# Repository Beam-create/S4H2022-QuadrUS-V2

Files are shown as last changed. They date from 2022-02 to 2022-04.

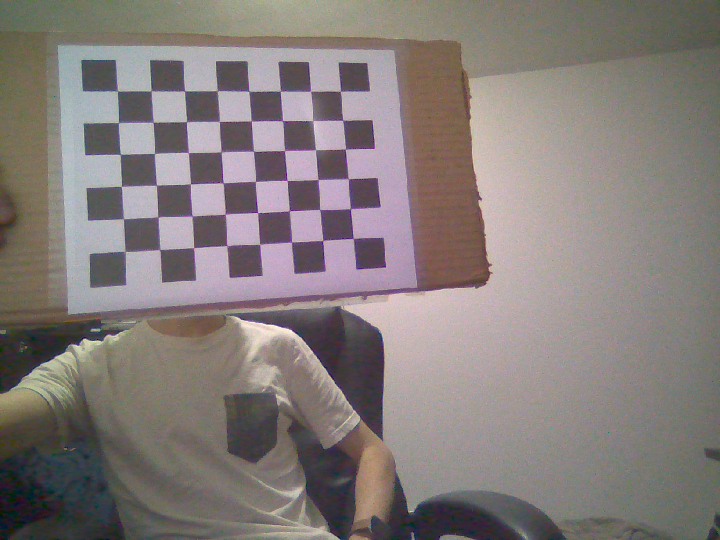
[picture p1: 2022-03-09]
VISION/CalibrationStereo/Images/Gauche/imgG22.png

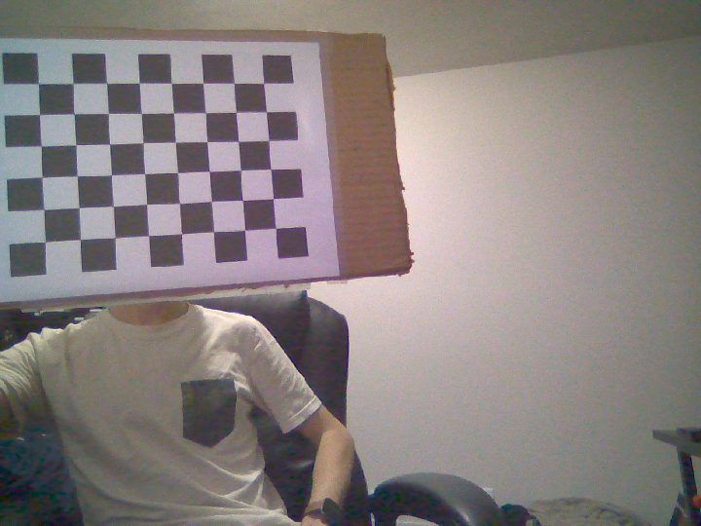
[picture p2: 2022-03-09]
VISION/CalibrationStereo/Images/Droite/imgD22.png

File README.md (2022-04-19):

# S4H2022-RufUS

### Robot-chien | UdeS-GRO
 

## Présentation du projet
<p align="center">
    	
    	<br>
    	
	<br>
	<a>Respectivement <strong>Antoine Waltz</strong>, <strong>Jordan Simard</strong>, <strong>Guillaume Blain</strong>, <strong>Mathieu Beaudoin</strong>, <strong>Christopher Pacheco</strong> et <strong>Nicolas Longchamps</strong></a>
</p>

<p align="center">
	
	<br>
</p>

RufUS est un robot collaboratif conçu et fabriqué par 6 étudiants en génie robotique à l'Université de Sherbrooke. Ce projet est fait dans le cadre du projet de la session 4.

Le but de ce projet est de construire un robot ayant la capacité de détecter, saisir puis rapporter un item. Pour ce faire, RufUS intègre une vision caméra, un bras robotique et une base mobile.

## Téléchargement du projet
1. Installez le fichier d'installation grâce à la commande ci-dessous:
 ```
 wget https://raw.githubusercontent.com/Beam-create/S4H2022-RufUS/main/Installation.sh
 ```
2. Exécutez le fichier grâce à cette commande:
 ```
 bash Installation.sh
 ```

> L'exécution du fichier permet d'installer automatiquement toutes les librairies ROS et les dépendances nécessaires au projet. Il permet aussi de configurer l'infrastructure ROS du projet. En effet, Un dossier sous le nom de rufus_ws (rufus workspace) contenant tous les éléments nécessaire au fonctionnement de la plateforme sera créé.
### Validation de l'installation
1. Ouvrir un terminal et exécutez cette commande:
```
gedit .bashrc
```
2. Allez à la fin du fichier
3. Validez que *source ~/rufus_ws/devel/setup.bash* ne se trouver par entre ( " " )
## Comment démarrer le projet
1. Suivre les instructions d'installation sur un ordinateur avec Ubuntu20.04.
2. Suivre les instructions d'installation de Ubuntu20.04 sur le Jetson Nano (Voir [Configuration du Jetson Nano](/VISION#configuration-du-jetson-nano))
3. Lorsque l'installation est terminée sur le Jetson Nano, configurez le hotspot (Voir [Création d'un hotspot](/ROS#création-dun-hotspot)).
4. Avec le hotspot configuré, connectez vous par SSH au Jetson Nano.
5. Une fois connecté, allez dans le dossier rufus_ws et exécutez une compilation du programme ROS :
```
cd ~/rufus_ws     
catkin_make
```
puis une fois compilé,
```
source devel/setup.bash
```
6. Ensuite, toujours sur le Jetson Nano avec la connexion SSH, lancez le programme *master* :
```
roslaunch rufus_master rufus_master.launch
```
7. Puis, avec l'ordinateur *remote*, lancez :
```
roslaunch rufus_remote rufus_remote.launch
```
puis, dans un autre terminal, lancez _rqt_ avec la commande :
```
rqt
```
Et le tour est joué! Vous obtiendrez ceci comme interface utilisateur :
<p align="center">
	
	<br>
</p>

**Troubleshooting**
Si des problèmes de connexion ont lieu, vérifiez que les adresses IP concordent avec les *launchfiles*.

## Table des matières
* Documentation
	* [Base](/FABRICATION/BASE#s4h2022-rufusbase)
		* [Fichiers CAD](/FABRICATION/BASE#fichers-cad)
		* [Comment fabriquer la base mobile](/FABRICATION/BASE#comment-fabriquer-la-base-mobile) 
			* [Liste des matériaux et composantes](/FABRICATION/BASE#liste-des-matériaux-et-composantes)
			* [Assemblage mécanique](/FABRICATION/BASE#assemblage-mécanique)
			* [Assemblage électrique](/FABRICATION/BASE#assemblage-électrique)
	* [Bras](/BRAS.md)
		* [Assemblage du bras robot](/BRAS.md#assemblage-du-bras-robot)
		* [Contrôle du bras robot](/BRAS.md#contrôle-du-bras-robot)
		* [Dépendances logicielles](/BRAS.md#dépendances-logicielles)
	* [Vision](/VISION#s4h2022-rufusvision)
		* [Matériel nécessaire](/VISION#matériel-nécessaire)
		* [Configuration du Jetson Nano](/VISION#configuration-du-jetson-nano)
			* [Installation de Ubuntu 20.04](/VISION#installation-de-ubuntu-2004)
			* [Installation des dépendances (vision)](/VISION#installation-des-dépendances)  
	* [Arduino](/ARDUINO#s4h2022-rufusarduino)
	* [ROS](/ROS#s4h2022-rufusros)
		* [Configuration du Jetson Nano](/ROS#configuartion-du-jetson-nano) 
			* [Création d'un hotspot](/ROS#création-dun-hotspot)
			* [Connexion par ssh](/ROS#connexion-au-jetson-nano-par-ssh) 
* [Licence](https://github.com/Beam-create/S4H2022-RufUS/blob/main/README.md#licence-mit)

### Licence MIT
Copyright 2022 RufUS

Permission is hereby granted, free of charge, to any person obtaining a copy of this software and associated documentation files (the "Software"), to deal in the Software without restriction, including without limitation the rights to use, copy, modify, merge, publish, distribute, sublicense, and/or sell copies of the Software, and to permit persons to whom the Software is furnished to do so, subject to the following conditions:

The above copyright notice and this permission notice shall be included in all copies or substantial portions of the Software.

THE SOFTWARE IS PROVIDED "AS IS", WITHOUT WARRANTY OF ANY KIND, EXPRESS OR IMPLIED, INCLUDING BUT NOT LIMITED TO THE WARRANTIES OF MERCHANTABILITY, FITNESS FOR A PARTICULAR PURPOSE AND NONINFRINGEMENT. IN NO EVENT SHALL THE AUTHORS OR COPYRIGHT HOLDERS BE LIABLE FOR ANY CLAIM, DAMAGES OR OTHER LIABILITY, WHETHER IN AN ACTION OF CONTRACT, TORT OR OTHERWISE, ARISING FROM, OUT OF OR IN CONNECTION WITH THE SOFTWARE OR THE USE OR OTHER DEALINGS IN THE SOFTWARE.

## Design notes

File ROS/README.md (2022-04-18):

# S4H2022-RufUS/ROS

## Configuration du Jetson Nano
### Création d'un hotspot
La création d'un réseau wi-fi dit "hotspot" sur un appareil permet à un ordinateur tiers de se connecter à cet appareil et d'avoir accès à l'internet sans fil si l'appareil recoit une connexion internet filaire. Par extension, cela permet à l'ordinateur tiers d'accéder au terminal de l'appareil par "ssh" afin de lancer des commandes (voir la section correspondante). Le but ici est donc de lancer les commandes ROS sur le Jetson Nano à partir d'un autre ordinateur sans connexion filaire reliant les deux appareils.
##### Méthode 1 (simple)
1. Aller dans la section "Wi-Fi" des paramètres de Ubuntu du Jetson Nano
2. Appuyer sur les trois petits points en haut à droite de la fenêtre, puis sélectionner "Allumer le point d'accès Wi-Fi..."

3. Assigner un nom au réseau (au choix), définir un mot de passe (au choix) et appuyer sur "Allumer"

4. Vérifier si le hotspot apparait parmi les réseaux disponible sur l'ordinateur, le cas échéant, s'y connecter

#### Méthode 2 (plus d'options)
1. Ouvrir un terminal de commande sur le Jetson Nano, puis taper la commande "nm-connection-editor": la fenêtre "Connexions réseau" devrait apparaître

2. Appuyer sur "+" en bas à gauche de la fenêtre pour ajouter un nouveau réseau

3. Sélectionner "Wi-Fi" dans les options de la fenêtre "Sélectionner un type de connexion", puis appuyer sur "Créer"

4. Modifier au minimum ces paramètres dans l'onglet "Wi-Fi":
	*   Assigner un nom à la connexion (au choix)
	*  Assigner un SSID (au choix)à
	* Sélectionner le mode "Hotspot"

5. Optionnel: Modifier les autres paramètres selon les besoins
6. Appuyer sur "Enregistrer"
7. Aller dans la section "Wi-Fi" des paramètres de Ubuntu du Jetson Nano
8. Appuyer sur les trois petits points en haut à droite de la fenêtre, puis sélectionner "Connexion à un réseau masqué..."

9. Sélectionner le hotspot créé en fonction du nom assigné à l'étape 4, puis appuyer sur "Se connecter"

10. Vérifier si le hotspot apparait parmi les réseaux disponible sur l'ordinateur, le cas échéant, s'y connecter

### Connexion au Jetson Nano par SSH
1. Ouvrir un terminal de commande sur le Jetson Nano et taper "ifconfig"
2. Noter l'adresse ip à côté de "inet" sous "wlan0" de la forme 10.x.x.x, par exemple 10.42.0.1
3. Ouvrir un terminal de commande sur l'ordinateur et taper "ssh <Nom du Jetson Nano>@<Adresse ip notée>", par exemple "ssh jetson@10.42.0.1"
4. Accepter les demandes d'accès et entrer le mot de passe du Jetson Nano le cas échéant

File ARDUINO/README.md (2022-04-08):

# S4H2022-RufUS/Arduino
On retrouve ici la documentation concernant le projet *platformIO*. Si vous n'êtes pas familier avec cet extension de *visual studio code* (vscode), nous vous recommendons de vous rendre sur la [page officielle](https://docs.platformio.org/en/latest/what-is-platformio.html) pour de plus amples informations. Il est recommendé de l'installer directement à partir de l'onglet extensions dans vscode.

## Configuration
Il suffit tout simplement d'ouvrir le dossier contenant le fichier *platformio.ini* dans vscode et de téléverser le fichier main.cpp dans votre arduino mega 2560.

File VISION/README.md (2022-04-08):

# S4H2022-RufUS/VISION
## Matériel nécessaire
- [ ] **Caméra stéréoscopique:**   [IMX219-83](https://www.waveshare.com/wiki/IMX219-83_Stereo_Camera) 
## Configuration du Jetson Nano
### Installation de Ubuntu 20.04 
D'ici la sortie d'une version de JetPack (OS de base du Jetson Nano) utilisant Ubuntu 20.04.

Suivre le [tutoriel de QEngineering](https://qengineering.eu/install-ubuntu-20.04-on-jetson-nano.html) afin d'installer et de configurer le Jetson Nano.

**Une image précompilée (qui ne nécessite pas de "*build from source*") est disponible [ici](https://github.com/Qengineering/Jetson-Nano-Ubuntu-20-image), par QEngineering également.**

On conseille l'image précompilée, qui ne prendra pas 6 heures de "*build*".
### Installation des dépendances
Pour les installations nécessaires (python3),

    pip3 install matplotlib numpy pillow imutils mediapipe 

#### Dual_Detect.py
Ce programme permet de détecter la présence d'un visage et d'une balle de jaune ou orange. Ensuite, par triangulation, la distance est évaluée et renvoyée en cm sur l'image.

    python3 DualDetect.py

#### test_vpi.py 
Ce programme évalue la disparité stéréoscopique et retourne une image de style *heatmap*. Il fonctionne pour le moment avec python2.7.

Afin de faire fonctionner la librairie VPI de NVIDIA pour l'utilisation de CUDA dans l'évaluation de la disparité, on doit créer un lien symbolique dans Ubuntu 20.04:

    cd /usr/lib/python2.7/dist-packages
    sudo ln -s /opt/nvidia/vpi1/lib64/python/vpi.so
Finalement, on doit modifier le fichier .bashrc afin d'éviter une erreur de dépendance :

**Afin d'ouvrir le fichier .bashrc:**

    sudo nano ~/.bashrc

Ajouter à la fin du .bashrc :

    export LD_PRELOAD=/usr/lib/aarch64-linux-gnu/libgomp.so.1
Sauvegarder et quitter le fichier. Le Jetson est maintenant prêt!

**Pour exécuter le programme test_vpi.py**

    python2 test_vpi.py

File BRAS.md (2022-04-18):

# S4H2022-RufUS/BRAS
## Liste des matériaux et composantes
- [ ] 1 x Servo DS3225  ([amazon](https://www.amazon.ca/-/fr/enti%C3%A8rement-m%C3%A9tallique-num%C3%A9rique-voitures-contr%C3%B4le/dp/B07NSG5WFQ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))
- [ ] 2 x Servo DS3218 ([amazon](https://www.amazon.ca/Servomoteur-num%C3%A9rique-%C3%A9tanche-voiture-contr%C3%B4le/dp/B07MDM1C3M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))
- [ ] 1 x Servo SG90 ([amazon](https://www.amazon.ca/-/fr/servomoteur-radiocommand%C3%A9-h%C3%A9licopt%C3%A8re-v%C3%A9hicules-compatible/dp/B097RD8RB7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))
## Assemblage du bras robot

[Instructions de montage du bras.pdf](https://github.com/Beam-create/S4H2022-RufUS/files/8430149/Instructions.de.montage.du.bras.pdf)

Voici le site sur lequel ces instructions sont basés : [lien](http://www.eezyrobots.it/eba_mk2.html)

Tout crédit pour le modèle utilisé se réserve à: Carlo Franciscone, daGHIZmo ([profil thingiverse]( https://www.thingiverse.com/daghizmo/designs)).

Certaines modifications au niveau du dimensionnement ont été apportés afin de répondre au besoin du projet RufUS: 
 1- Assise de servo moteur.
 2- Longueur des membrures.

Lien pour la license CC: https://www.thingiverse.com/thing:1454048

## Contrôle du bras robot

### Cinématique inverse
Afin de se rendre à la position cartésienne de la balle (position détecté par la caméra), une cinématique inverse a été modélisée à partir des schéma suivant :

1- Vue de coter du bras du robot :
vue_coter2

2- Vue de dessus du bras du robot : 
vue_dessus2

Les équations tirés de ces schémas sont :
<p align="center">
    
    <br>
    
    <br>
    
</p>

Avec la position en "x" et en "z" de la balle, il est possible de déterminer l'angle de rotation du joint 1. Par la suite, une fois que l'angle 1 est connu, il est possible d'utiliser le "solver" "nsolve" de python pour résoudre le système à deux équations et 2 inconnues pour trouver la valeur des angles pour les joints 2 et 3. Les valeurs de pi/2 et 0 dans le "nsolve" représente les valeurs des angles initiales en radians des joints 2 et 3 respectivement, ce qui permet d'accélérer la résolution du système d'équation.

### Calibration des servo
Afin de bien modéliser le comportement réel des servos moteurs, une calibration est utilisée dans le but d'extraire une fonction approximative du signal PWM en fonction de l'angle désiré. 

Les étapes de calibration sont :

 1- Création d'une série de données [angles_réels, PWM_envoyés] pour chaque servo.

 2- Selon l'allure de la courbe, on utilise une fonction de linéarisation à plusieurs coefficients afin d'approximer la courbe de données discrètes. 

 3- Mesurer les erreurs quadratiques afin d'assurer une précision adéquate.

 4- Modéliser la fonction de *writeMicroseconds()* selon la fonction linéarisée obtenue.

> Pour ce faire, Matlab/Python sont de bons outils d'analyse numérique. 

## Dépendances logicielles
Pour le fonctionnement bas-niveau du bras, le code c++ doit inclure la librairie externe suivante:

1- [Servo.h](https://github.com/arduino-libraries/Servo), librairie Arduino pour le contrôle de servo moteur selon une commande PWM ou un angle.

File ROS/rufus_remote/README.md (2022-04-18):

# Fonctionnement du package

Le package rufus_remote doit être présent dans l'ordinateur connecté au master
Ce package contient les scripts pour le contrôle de la base et du bras, et le launch file pour se connecter au robot

## Nodes:

Le package contient le cde source des nodes suivantes:
- base_teleop
- bras_teleop

## Launch files

Le launch file pour connecter l'ordinateur au robot est:
rufus_remote.launch

La commande pour partir le laucnh file est:

    roslaunch rufus_remote rufus_remote.launch

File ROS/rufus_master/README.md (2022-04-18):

# Fonctionnement du package

Le package rufus_master doit être téléchargé dans le Jetson Nano. Ce package contient les scripts pour le contrôle de la base et le launch file pour démarer le robot

## Messages:

Le package crée les messages suivants:

-   bras_commands.msg
-   Feedback_arduino_msgs.msg
-   Rufus_base_msgs.msg

## Nodes:

Le package contient le cde source des nodes suivantes:

-   base_control_node

## Launch files

Le launch file pour démarrer le robot est:
rufus_master.launch

La commande pour partir le laucnh file est: 

    roslaunch rufus_master rufus_master.launch

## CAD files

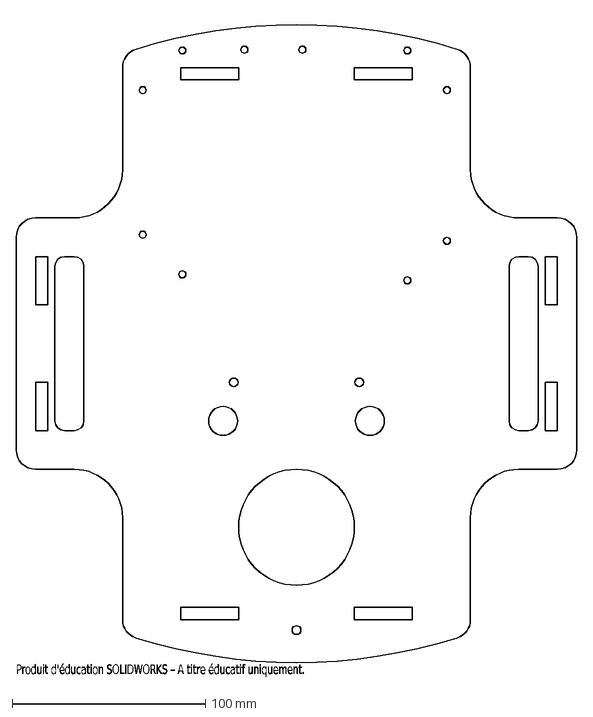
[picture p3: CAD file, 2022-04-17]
FABRICATION/BASE/DÉCOUPER/S4H2022_Base_002.DXF
Produit d'éducation SOLIDWORKS – A titre éducatif uniquement.

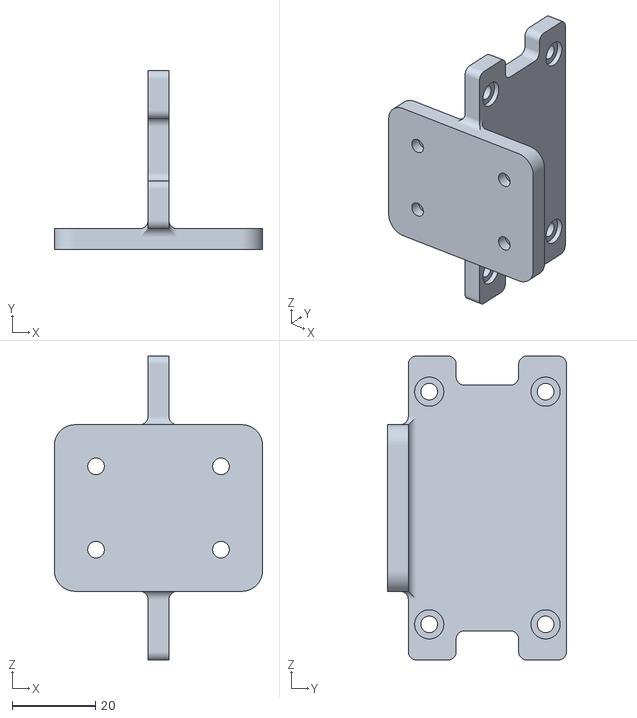
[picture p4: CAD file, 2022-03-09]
FABRICATION/BASE/IMPRIMER/S4H2022_Base_drive_bracket_V3.STL
50.0 x 43.0 x 73.0

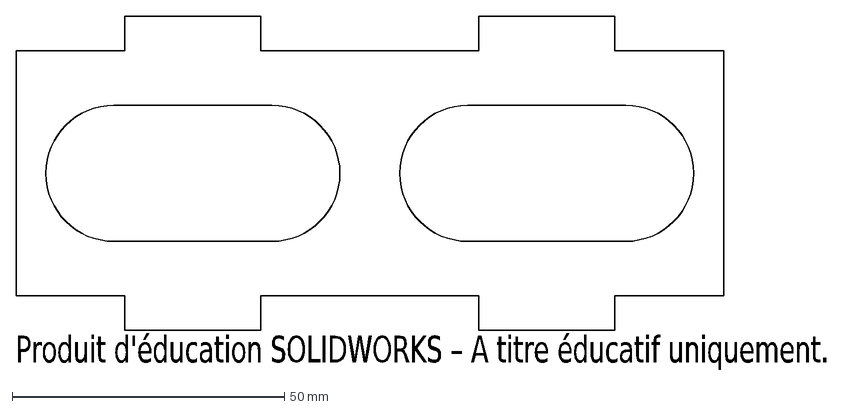
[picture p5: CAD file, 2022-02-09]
FABRICATION/BASE/DÉCOUPER/S4H2022_Base_004.DXF
Produit d'éducation SOLIDWORKS – A titre éducatif uniquement.

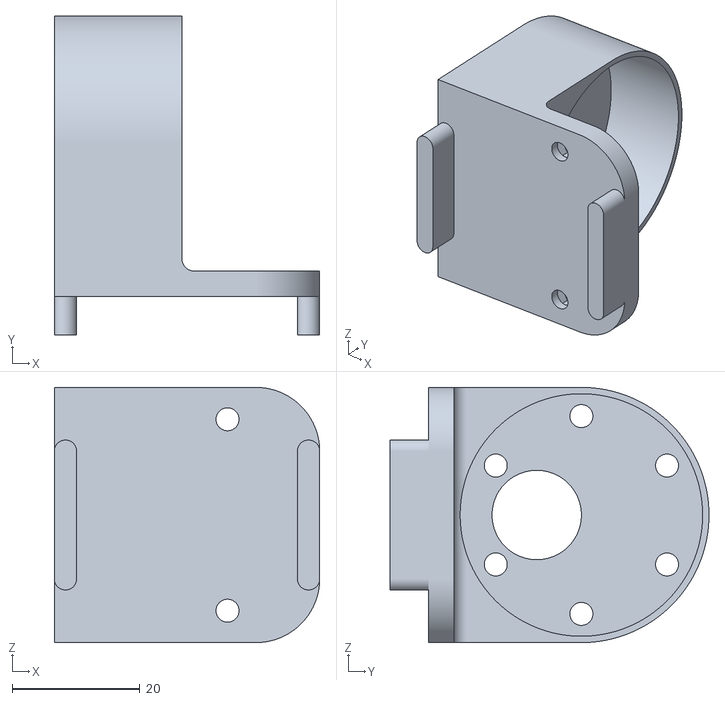
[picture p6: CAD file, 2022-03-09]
FABRICATION/BASE/IMPRIMER/S4H2022_Base_motor_mount.STL
41.6 x 50.0 x 40.0

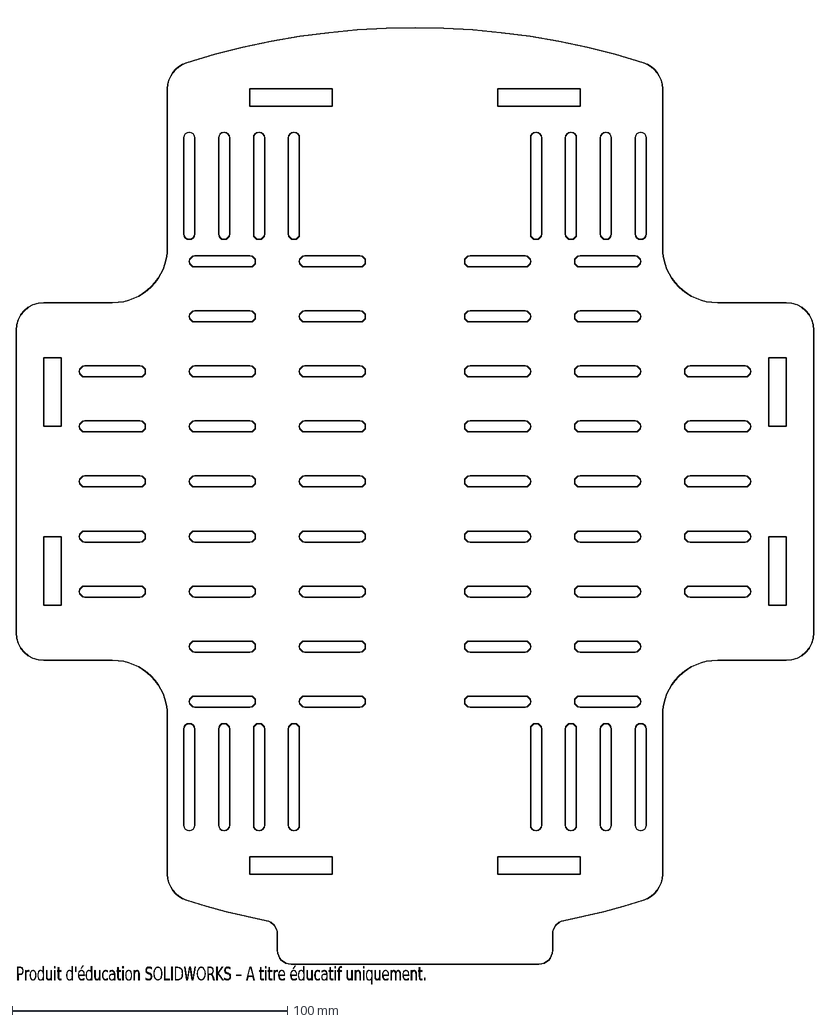
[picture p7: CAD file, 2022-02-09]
FABRICATION/BASE/DÉCOUPER/S4H2022_Base_001.DXF
Produit d'éducation SOLIDWORKS – A titre éducatif uniquement.

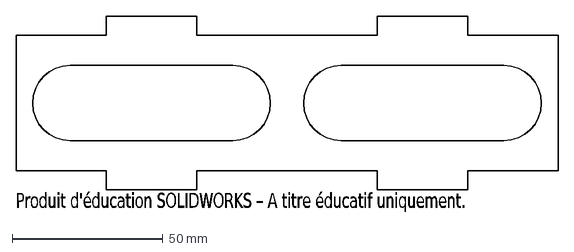
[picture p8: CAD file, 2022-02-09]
FABRICATION/BASE/DÉCOUPER/S4H2022_Base_003.DXF
Produit d'éducation SOLIDWORKS – A titre éducatif uniquement.

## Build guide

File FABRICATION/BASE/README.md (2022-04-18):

# S4H2022-RufUS/BASE
## [Fichiers CAD](https://github.com/Beam-create/S4H2022-RufUS/tree/main/CAD)

## Comment fabriquer la base mobile
Base_mec_cool

La base mobile est faite de matériaux et de composants faciles à trouver. Sa réalisation nécessite l'accès à une **découpeuse laser à bois**, une **imprimante 3d** et des outils électroniques tels qu'un **fer à souder**, un **multimètre** et une **source d'alimentation 12V** (optionnel).

### Liste des matériaux et composantes
***
#### Mécanique
- [ ]  Vis M3 X 0.5 
- [ ] Écrous M3 X 0.5 
- [ ] 2' X 3' X 1/4" contre-plaqué
- [ ] Roue Mecanum 80mm ([robotshop](https://www.robotshop.com/ca/en/80mm-mecanum-wheel-kit-4x.html))
- [ ] Moteur Pololu 50:1 12VDC  ([pololu](https://www.pololu.com/product/4753))
- [ ] Moyeu Servocity 1/4"  ([servocity](https://www.servocity.com/0-250-0-770-set-screw-hub/))
- [ ] Support moteur Pololu ([pololu](https://www.pololu.com/product/1084))

### Électrique
- [ ] Arduino Mega 2560 ([arduino](https://store-usa.arduino.cc/products/arduino-mega-2560-rev3))
- [ ] Contrôleur Cytron MD13s ([cytron](https://www.cytron.io/p-13amp-6v-30v-dc-motor-driver))
- [ ] Convertisseur DC-DC ([amazon](https://www.amazon.ca/Yizhet-Module-dalimentation-r%C3%A9glable-LM2596/dp/B08Q2YKJ6Q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))
- [ ] Ensemble connecteurs Dupont ([amazon](https://www.amazon.ca/Yangoutool-Dupont-connecteurs-cliquet-JST-XH/dp/B07X9MJ8G2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))
- [ ] Ensemble espaceur PCB ([amazon](https://www.amazon.ca/Litorange-entretoises-hexagonales-femelle-circuit/dp/B07TP2YYQB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))
- [ ] Fil 22 awg ([robotshop](https://www.robotshop.com/ca/fr/kit-fils-pvc-noyau-solide-plusivo-22awg-6-couleurs-10-m-chacun.html))
- [ ] Pin header([amazon](https://www.amazon.ca/-/fr/10-Paire-femelle-broches-Connecteur-Arduino/dp/B019WOPOHI/ref=sr_1_10?__mk_fr_CA=ÅMÅŽÕÑ&crid=2QZMUE8YLUWN3&keywords=pin+header&qid=1649268265&sprefix=pin+header%2Caps%2C54&sr=8-10))
- [ ] Connecteur bornier([amazon](https://www.amazon.ca/-/fr/gp/product/B07H5G7GC6/ref=ppx_yo_dt_b_asin_title_o07_s00?ie=UTF8&th=1))
- [ ] Connecteur grove([amazon](https://www.amazon.ca/-/fr/WOWOONE-connecteurs-femelles-Micro-broches/dp/B08RHGT3W3/ref=sr_1_38?__mk_fr_CA=ÅMÅŽÕÑ&crid=2IVHVETWWB96F&keywords=grove+connectors+4&qid=1649268329&sprefix=grove+connectors+4%2Caps%2C57&sr=8-38))

### Assemblage mécanique
***
Ce [dossier](https://github.com/Beam-create/S4H2022-RufUS/tree/main/CAD) contient plus de détails sur l'assemblage, ainsi que les STL et DXF pour fabriquer les pièces.
#### Assemblage châssis
S4H2022_Base_000

#### Assemblage roues
S4H2022_Base_wheel_assy

### Assemblage électrique
***
Base_elec

#### Circuit imprimé


Un PCB a été concu afin de facilliter les branchements électriques. Toute l'information reliée au sens des branchements est indiqué directement sur le circuit. Pour se procurer le PCB, il suffit d'aller sur un site de commande de pcb en ligne (ex: [jlcpcb.com](https://jlcpcb.com/VGB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)) et d'y téléverser le dossier compressé  [*PCB_Production.zip*](https://github.com/Beam-create/S4H2022-RufUS/files/8502373/PCB_Production.zip). Aucun paramètre par défaut n'est à modifier.

> **IMPORTANT**: Pour la section de pin à souder située à droite du Arduino Mega, il faut SEULEMENT souder les pins entourées en rouge.

##### Configuration des convertisseurs DC-DC
1. Brancher une source de tension (12V) à l'entré du convertisseur et brancher un multimetre à sa sortie
2. À l'aide d'un tournevis, vous devez changer la tension de sortie à 5V et à 6.8V pour deux convertisseurs que vous pourrez ensuite placer sur le pcb aux endroits indiqués.

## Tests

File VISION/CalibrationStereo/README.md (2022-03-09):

# Calibration de la caméra stéréoscopique
 1. Se rendre dans le répertoire **CalibrationStereo**
	`cd CalibrationStereo`
## Acquisition
Afin de calibrer la caméra stéréoscopique, on doit utiliser un échiquier de calibration.
Après l'impression sur une feuille 8½x11, on puet exécuter la calibration avec :
   ` python3 Acquisition.py`
Afin d'enregistrer une image, on appuie sur la touche `ESPACE`, pour quitter l'application, on appuie sur la touche `q` ou `ESC`.

## Calibration
Lorsque la totalité du champ de vision de la caméra a été couvert par des photos de l'échiquier, on puet poursuivre avec la calibration.
La calibration consiste à premièrement rectifier les images individuellement afin d'éliminer la distorsion causée par la lentille, puis à calibrer la stéréoscopie.
Il suffit d'exécuter :

    python3 StereoCalibration.py
Les données de calibration seront ainsi enregistrées sous **stereoMap.xml**.

## Test de la calibration
Afin d'évaluer la qualité de la calibration, on peut exécuter le programme **StereoVision_RectificationTest.py**.
`python3 StereoVision_RectificationTest.py`

Si la calibration est erronée, on peut refaire l'acquisition. Le processus est très itératif.

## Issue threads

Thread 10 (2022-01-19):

Contrôle en vitesse et position PID

Beam-create, 2022-01-19:

Chrispako990210, 2022-01-26:
Nb d'heures :
Risques :
Problèmes :

Chrispako990210, 2022-02-16:
This issue should be deleted, it is not implemented in the project dev.

Closed 2022-02-16.

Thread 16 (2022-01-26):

Stabilisateur mécanique pour la vision

NicoLongfield, 2022-01-26:
Concevoir un "gimbal" qui stabilisera la caméra stéréoscopique :

- [ ] Modélisation

- [ ] Assemblage

- [ ] Acquisition de données (accéléromètre)

- [ ] Prototypage électrique

- [ ] Développement logiciel de contrôle

NicoLongfield, 2022-01-26:
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

Closed 2022-02-23.

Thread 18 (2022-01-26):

Acquisition des données de l'accéléromètre

NicoLongfield, 2022-01-26:

Blain354, 2022-02-01:
le gyro sur la caméra fonctionne sur l'environnement linux (pi/jetson) mais pas sur arduino donc on utilise maintenant un gyro indépendant de la caméra qui est fonctionnel avec arduino

Closed 2022-02-16.

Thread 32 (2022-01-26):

Construire l'environnement de simulation ROS

Chrispako990210, 2022-01-26:

simj5121, 2022-01-26:
Nb d'heures : (Sem. 24-28 janv 0 heures),
Risques :
-Intégration des CAD
-Frottement entre les joints
Problèmes :

simj5121, 2022-02-01:
L'environnement global est terminer :
-Possible de faire bouger de manière indépendante chaque joint d'un robot simple à 3 axes

Closed 2022-02-01.

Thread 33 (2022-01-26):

Setup les CAD dans Gazebo + appliquer les  liens géométriques

Chrispako990210, 2022-01-26:

Chrispako990210, 2022-01-26:
Nb d'heures :
Risques : Bug d'intégration avec l'environnement de simulation
Problèmes :

Closed 2022-03-15.

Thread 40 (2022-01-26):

Faire une description gazebo de la base

Beam-create, 2022-01-26:

Beam-create, 2022-02-12:
Risque :  La base n'affiche pas complètement dans gazebo. Les roues ne sont pas affichés, mais aucun message d'erreur n'est affiché. Le debuggage peut prendre plus de temps que prévu

Closed 2022-03-09.

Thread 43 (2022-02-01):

Assemblage électrique de la base

Beam-create, 2022-02-01:

Beam-create, 2022-02-01:
BUG: Manque le convertisseur dc-dc 12v vers 6.8v

Je regarde avec François Ferland pour une solution. L'université va peut-être acheter des convertisseur puis nous les prêter.

Beam-create, 2022-02-01:
Difficile d'accès au compartiment électrique, il va falloir couper le châssis en bois et faire une barre de renforcement amovible. Il peut y avoir des complications pour couper ou pour solidifier le châssis.

Closed 2022-02-16.

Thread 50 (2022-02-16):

Redesign et print de la pince

Chrispako990210, 2022-02-16:

Closed 2022-02-16.

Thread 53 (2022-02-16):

Implémentation ros serial / rospy pour la com, jetson et arduino

Chrispako990210, 2022-02-16:

simj5121, 2022-03-14:
Création des nodes et des topics pour la communication avec le bras robot (position de la balle vue par la caméra et angles des joints du bras robot)

simj5121, 2022-03-22:
Problème : Intégration d'une librairie "custom" python dans ros -­> Résolue

Closed 2022-04-06.

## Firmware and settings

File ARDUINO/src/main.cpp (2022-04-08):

/* 
 * GRO 400 - Conception agile et ouverte en robotique
 * Code de démarrage
 * Auteurs: Antoine Waltz et al     
 * date: 22 février 2022
*/

/*------------------------------ Librairies ---------------------------------*/

#include <Arduino.h>
#include "rufus_lib/motor.h"
#include "rufus_lib/pid.h"
#include "rufus_lib/Bras_servo_control.h"
#include "Servo.h"
#include <ros.h>
#include <rufus_master/Rufus_base_msgs.h>
#include <rufus_master/bras_commands.h>
#include <std_msgs/String.h>
#include <rufus_master/Feedback_arduino_msgs.h>

/*------------------------------ Constantes ---------------------------------*/

#define BAUD            9600      // Fréquence de transmission serielle

/*---------------------------- variables globales ---------------------------*/
 
 // ENC_A: Fil jaune de l'encodeur, soit 2,3,18 ou 19
int FL_ENC_A_pin = 19;
int FR_ENC_A_pin = 18;
int BL_ENC_A_pin = 2;
int BR_ENC_A_pin = 3;

// ENC_B: Fil blanc de l'encodeur, entre 22 et 53 (30,32,34,36)
int FL_ENC_B_pin = 37;
int FR_ENC_B_pin = 35;
int BL_ENC_B_pin = 31;
int BR_ENC_B_pin = 33;

// ENC_Vcc: Fil bleu de l'encodeur, 3.5-20 V
// ENC_GND: Fil vert de l'encodeur

// DIR: Fil jaune du contrôleur de moteur, entre 22 et 53 (22,24,26,28)
int FL_DIR_pin = 27;
int FR_DIR_pin = 29;
int BL_DIR_pin = 23;
int BR_DIR_pin = 25;

// PWM: Fil blanc du contrôleur de moteur, entre 4 et 13 (4,5,6,7)
int FL_PWM_pin = 5;
int FR_PWM_pin = 4;
int BL_PWM_pin = 7;
int BR_PWM_pin = 6;

// Pin gimbal
int gimbal_pin = 8;


// Déclaration des objets moteur
motor FL_motor(FL_ENC_A_pin, FL_ENC_B_pin, FL_DIR_pin, FL_PWM_pin);
motor *FL = &FL_motor;
motor FR_motor(FR_ENC_A_pin, FR_ENC_B_pin, FR_DIR_pin, FR_PWM_pin);
motor *FR = &FR_motor;
motor BL_motor(BL_ENC_A_pin, BL_ENC_B_pin, BL_DIR_pin, BL_PWM_pin);
motor *BL = &BL_motor;
motor BR_motor(BR_ENC_A_pin, BR_ENC_B_pin, BR_DIR_pin, BR_PWM_pin);
motor *BR = &BR_motor;

// Déclaration de l'objet PID
PID pid(*FL, *FR, *BL, *BR);

// Déclaration de l'objet Gimbal
Servo gimbal;

// Declaration de l'objet Bras et autre variables
Bras_servo_control bras;
const long interpolTime = 7;
unsigned long currentTime;

// ROS
ros::NodeHandle nh;
rufus_master::Feedback_arduino_msgs feedback_msg;

/*------------------------- Prototypes de fonctions -------------------------*/

void readEncoderFL();
void readEncoderFR();
void readEncoderBL();
void readEncoderBR();
void commandCB(const rufus_master::Rufus_base_msgs& motor_cmd);
void brasCB(const rufus_master::bras_commands& bras_cmd);


/*---------------------------- fonctions "Main" -----------------------------*/

ros::Subscriber<rufus_master::Rufus_base_msgs> motor_sub("/rufus/base_arduino", commandCB);
ros::Subscriber<rufus_master::bras_commands> bras_sub("/rufus/bras_arduino", brasCB); // Get les commands via le topic envoyer par bras_teleop et IK
ros::Publisher arduino_feedback("/rufus/arduino_feedback",&feedback_msg);

void setup() {
  // Serial.begin(BAUD);

  // Setup ros, goes first always!
  nh.getHardware()->setBaud(57600);
  nh.initNode();
  nh.advertise(arduino_feedback);
  nh.subscribe(bras_sub);
  nh.subscribe(motor_sub);
  nh.negotiateTopics();


  // Fonctions qui assigne les pins à lire et les fonctions pour lire les encodeurs
  // attachInterrupt: 2, 3, 18, 19, 20, 21 (pins 20 & 21 are not available to use for interrupts while they are used for I2C communication)
  attachInterrupt(digitalPinToInterrupt(FL_motor.getPin(FL_motor._ENC_A)), readEncoderFL, RISING);
  attachInterrupt(digitalPinToInterrupt(FR_motor.getPin(FR_motor._ENC_A)), readEncoderFR, RISING);
  attachInterrupt(digitalPinToInterrupt(BL_motor.getPin(BL_motor._ENC_A)), readEncoderBL, RISING);
  attachInterrupt(digitalPinToInterrupt(BR_motor.getPin(BR_motor._ENC_A)), readEncoderBR, RISING);
  pid.setGains(1, 0.1, 0.05);
  gimbal.attach(gimbal_pin);
  gimbal.write(90); // Angle zéro à trouver, en degré

  bras.initServos();
  bras.drop();
  bras.goToHome();
}

void loop() {
  arduino_feedback.publish(&feedback_msg);
  nh.spinOnce();
  delay(10);
}

/*---------------------------Definition de fonctions ------------------------*/
// Fonctions qui appelle la fonction de lecture de la position de l'encodeur
void readEncoderFL(){
  FL_motor.readEncoder();
}
void readEncoderFR(){
  FR_motor.readEncoder();
}
void readEncoderBL(){
  BL_motor.readEncoder();
}
void readEncoderBR(){
  BR_motor.readEncoder();
}

void commandCB(const rufus_master::Rufus_base_msgs& motor_cmd)
{
  float cmd_FL = motor_cmd.motor_FL;
  float cmd_FR = motor_cmd.motor_FR;
  float cmd_BL = motor_cmd.motor_BL;
  float cmd_BR = motor_cmd.motor_BR;

  FL_motor.setPWM(cmd_FL);
  FR_motor.setPWM(cmd_FR);
  BL_motor.setPWM(cmd_BL);
  BR_motor.setPWM(cmd_BR);
  
  //Ajouter les fonctions pour faire tourner les moteurs en fonction des cmd_XX
  // pid.run(cmd_FL, cmd_FR, cmd_BL, cmd_BR);

  feedback_msg.motor_FL = cmd_FL;
  feedback_msg.motor_FR = cmd_FR;
  feedback_msg.motor_BL = cmd_BL;
  feedback_msg.motor_BR = cmd_BR;

}

void brasCB(const rufus_master::bras_commands& bras_cmd){ // Callback not triggered, A DEBUG!

  // Tsansfert des angles dans des variables locals
  float angles[nbJoints];
  angles[0] = bras_cmd.q1;
  angles[1] = bras_cmd.q2;
  angles[2] = bras_cmd.q3;


  bool isDone = false;
  float smoothAngles[nbJoints];
  if(bras_cmd.mode){
    bras.drop();
    while(!isDone){
      for (int i=0; i<nbJoints; i++)
      {
        smoothAngles[i] = (angles[i]*0.03) + (bras.prevAngles[i]*0.97);
        bras.prevAngles[i] = smoothAngles[i];
      }
      bras.goTo(smoothAngles);
      delay(7);
      if((round(smoothAngles[0]*100)/100.0) == angles[0] && (round(smoothAngles[1]*100)/100.0) == angles[1] && (round(smoothAngles[2]*100)/100.0) == angles[2]) // Sync once all 3 values have reached
      {
        isDone = true;
        bras.setPrevAngles(smoothAngles);
        // Serial.println("GOAL has been reached!"); //debugging
      }
    }
  }
  else{
    bras.goTo(angles);
  }
  // Check le state de leffecteur
  if(bras_cmd.effector){
    bras.pick();
    feedback_msg.effector = bras.isPick;
  }
  else{
    bras.drop();
    feedback_msg.effector = false;
  }

  // Gimbal control
  gimbal.write(bras_cmd.gimbalAng);

  
  feedback_msg.q1 = angles[0];
  feedback_msg.q2 = angles[1];
  feedback_msg.q3 = angles[2];
}

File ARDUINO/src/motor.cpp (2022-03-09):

/*
Projet S4 GRO 2022
Class to control Pololu 50:1 Metal Gearmotor 37Dx70L mm 12V 
with 64 CPR Encoder and with Cytron 13Amp 6V-30V DC Motor Driver 
on Arduino Mega 2560
@author Antoine Waltz et al
@version 1.0 09/02/2022
*/

#include "rufus_lib/motor.h"

motor::motor(){
    /*
    Constructeur par défaut qui assigne une valeur aux pins
    */
    _ENC_A_pin = -1;
    _ENC_B_pin = -1;
    _DIR_pin = -1;
    _PWM_pin = -1;
}
motor::motor(int ENC_A_pin, int ENC_B_pin, int DIR_pin, int PWM_pin){
    /*
    Constructeur qui vérifie la validité des pins entrées en paramètres et qui les assigne à ses attributs
    */
    if (motor::checkPins(ENC_A_pin, 1)){_ENC_A_pin = ENC_A_pin;}
    else{_ENC_A_pin = -1;}
    if (motor::checkPins(ENC_B_pin, 2)){_ENC_B_pin = ENC_B_pin;}
    else{_ENC_B_pin = -1;}
    if (motor::checkPins(DIR_pin, 3)){_DIR_pin = DIR_pin;}
    else{_DIR_pin = -1;}
    if (motor::checkPins(PWM_pin, 4)){_PWM_pin = PWM_pin;}
    else{_PWM_pin = -1;}
    motor::init();
}
motor::~motor(){
    /*
    Destructeur par défaut
    */
}
void motor::init(){
    /*
    Fonction qui initialise les pins sur l'Arduino
    */
    pinMode(motor::getPin(_ENC_A),INPUT);
    pinMode(motor::getPin(_ENC_B),INPUT);
    pinMode(motor::getPin(_DIR),OUTPUT);
    pinMode(motor::getPin(_PWM),OUTPUT);
}
bool motor::checkPins(int pin, int arg_nb){
    /*
    Fonction qui prend en paramètre une pin et son type selon 4 cas et qui vérifie si la pin fait partie des options disponible, retourne un booléen
    */
    switch (arg_nb){
        case 1:
            if (pin == 2 || pin == 3 || pin == 18 || pin == 19){
                return true;
            }
            else{
                Serial.println("Invalid pin number for _ENC_A_pin, choose either 2,3,18 or 19");
                return false;
            }
        case 2:
            if (pin >= 22 && pin <= 53){
                return true;
            }
            else{
                Serial.println("Invalid pin number for _ENC_B_pin, choose a pin between 22 and 53");
                return false;
            }
        case 3:
            if ((pin >= 22 && pin <= 53) || (pin >= 2 && pin <= 9) ){
                return true;
            }
            else{
                Serial.println("Invalid pin number for _DIR_pin, choose a pin between 22 and 53");
                return false;
            }
        case 4:
            if (pin >= 4 && pin <= 13){
            return true;
            }
            else{
                Serial.println("Invalid pin number for _PWM_pin, choose a pin between 4 and 13");
                return false;
            }
        default:
            Serial.println("Invalid pin number argument, choose between 1 and 4");
            return false;
        }
}
bool motor::safeCheck(){
    /*
    Fonction qui permet de vérifier si les pins ont bel et bien été assignées
    */
    if (motor::getPin(_ENC_A) == -1 || motor::getPin(_ENC_B) == -1 || motor::getPin(_DIR)== -1 || motor::getPin(_PWM) == -1) {return false;}
    else {return true;}
}
int motor::getPin(char _pinName[11]){
    /*
    Fonction qui retourne la valeur de la pin demandée
    */
    if (_pinName == _ENC_A){
        return _ENC_A_pin;
    }
    else if (_pinName == _ENC_B){
        return _ENC_B_pin;
    }
    else if (_pinName == _DIR){
        return _DIR_pin;
    }
    else if (_pinName == _PWM){
        return _PWM_pin;
    }
    else{
        Serial.println("Invalid pin name, choose either _ENC_A_pin, _ENC_B_pin, _DIR_pin or _PWM_pin");
        return -1;
    }
}
void motor::getPins(){
    /*
    Fonction qui affiche la valeur de toutes les pins
    */
    Serial.print(_ENC_A);
    Serial.print(" : ");
    Serial.println(_ENC_A_pin);
    Serial.print(_ENC_B);
    Serial.print(" : ");
    Serial.println(_ENC_B_pin);
    Serial.print(_DIR);
    Serial.print(" : ");
    Serial.println(_DIR_pin);
    Serial.print(_PWM);
    Serial.print(" : ");
    Serial.println(_PWM_pin);
}
void motor::readEncoder(){
    /*
    Fonction qui enregistre la position de l'encodeur sur un tour
    */
    if (digitalRead(_ENC_B_pin) > 0){
        encoder_pos++;
        }
    else {
        encoder_pos--;
        }
    if (encoder_pos >= encoder_max_pos){
        nb_rotation++;
        encoder_pos = encoder_pos - encoder_max_pos;
    }
    else if (encoder_pos <= -encoder_max_pos){
        nb_rotation--;
        encoder_pos = encoder_pos + encoder_max_pos;
    }
}
void motor::resetEncoder(){
    /*
    Fonction qui remet à zéro la position de l'encodeur
    */
    encoder_pos = 0;
    nb_rotation = 0;
}
int motor::getEncoderPos(){
    /*
    Fonction qui retourne la position de l'encodeur
    */
    return encoder_pos;
}
int motor::getNbRotation(){
    /*
    Fonction qui retourne le nombre de tours complets
    */
    return nb_rotation;
}
int motor::getEncoderPosTotal(){
    /*
    Fonction qui retourne la position absolue de l'encodeur depuis la dernière mise à zéro
    */
    return nb_rotation*encoder_max_pos + encoder_pos;
}
int motor::getResetEncoderPos(){
    /*
    Fonction qui retourne la position de l'encodeur sur un tour et qui réinitialise l'encodeur
    */
    int pos = motor::getEncoderPosTotal();
    motor::resetEncoder();
    return pos;
}
void motor::setPWM(float speed){
    /*
    Fonction qui permet de faire tourner le moteur selon un ratio de vitesse entre -1 et 1
    */
    set_speed = speed;
    int pwm = abs(speed*255.0f); // Change speed to unsigned integer
    // Switching polarity on DIR_PIN to change motor direction
    if (speed > 0) {
        digitalWrite(_DIR_pin, LOW);
    } else {
        digitalWrite(_DIR_pin, HIGH);
    }
    // SetPWM value
    analogWrite(_PWM_pin, (pwm > 255) ? 255 : static_cast<uint8_t>(pwm));
}
double motor::getMeanSpeed(){
    /*
    Fonction qui calcule et retourne la vitesse moyenne du moteur sur un intervalle de temps
    */
    int mean_time = 10; // ms, Temps entre deux lectures de l'encodeur pour calculer la vitesse moyenne
    int pos1 = motor::getEncoderPosTotal();
    delay(mean_time);
    int pos2 = motor::getEncoderPosTotal();
    return (double)((pos2-pos1))/(((mean_time))/1000.0)*pulse_per_seconds_to_unit_speed;
}

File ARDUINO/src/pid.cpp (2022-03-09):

/*
Projet S4 GRO 2022
Class to control Pololu 50:1 Metal Gearmotor 37Dx70L mm 12V 
with 64 CPR Encoder and with Cytron 13Amp 6V-30V DC Motor Driver 
on Arduino Mega 2560
@author Antoine Waltz et al
@version 1.0 09/02/2022
*/

#include "rufus_lib/pid.h"

PID::PID(motor &FL_motor, motor &FR_motor, motor &BL_motor, motor &BR_motor){
    _FL_motor = &FL_motor;
    _FR_motor = &FR_motor;
    _BL_motor = &BL_motor;
    _BR_motor = &BR_motor;
}
PID::~PID(){
    
}
void PID::setGains(float kp, float ki, float kd){
    Kp_ = kp; Ki_ = ki; Kd_ = kd;
}
void PID::reset(int motor_id){
    switch(motor_id){
        case 1:
            eIntegral_FL = 0;
            ePrevious_FL = 0;
            lastMeasureTime_FL = millis();
        case 2:
            eIntegral_FR = 0;
            ePrevious_FR = 0;
            lastMeasureTime_FR = millis();
        case 3:
            eIntegral_BL = 0;
            ePrevious_BL = 0;
            lastMeasureTime_BL = millis();
        case 4:
            eIntegral_BR = 0;
            ePrevious_BR = 0;
            lastMeasureTime_BR = millis();
    }
}
void PID::run(float cmd_FL,float cmd_FR,float cmd_BL,float cmd_BR){
    // Serial.println("Entré dans pid.run()");
    if (cmdPrevious_FL != cmd_FL){
        reset(1);
        atGoal_FL = false;
        atGoal_ = false;
        cmdPrevious_FL = cmd_FL;
    }
    else if (cmdPrevious_FR != cmd_FR){
        reset(2);
        atGoal_FR = false;
        atGoal_ = false;
        cmdPrevious_FR = cmd_FR;
    }
    else if (cmdPrevious_BL != cmd_BL){
        reset(3);
        atGoal_BL = false;
        atGoal_ = false;
        cmdPrevious_BL = cmd_BL;
    }
    else if (cmdPrevious_BR != cmd_BR){
        reset(4);
        atGoal_BR = false;
        atGoal_ = false;
        cmdPrevious_BR = cmd_BR;
    }
    // Serial.println("Vérification des commandes faite");
    // variables();
    //if (!atGoal_){
        // Serial.println("if (!atGoal_)");
        //if(!atGoal_FL){
            // Serial.println("if (!atGoal_FL)");
            double FL_error = cmd_FL - _FL_motor->getMeanSpeed();
            // Serial.println(FL_error);
            // Serial.println("Calcul de FL_error");
            Serial.println(FL_error);
            if(fabs(FL_error)<epsilon_){
                // Serial.println("if fabs(FR_error)<epsilon_)");
                atGoal_FL = true;
                _FL_motor->setPWM(cmd_FL);
            }
            else{
                // Serial.println("Entrée dans (*_FL_motor)->setPWM(computeCommand(1,FL_error))");
                _FL_motor->setPWM(computeCommand(1,FL_error));
                // Serial.println("(*_FL_motor)->setPWM(computeCommand(1,FL_error)) Fait!");
            }
        //}
        //if(!atGoal_FR){
            // Serial.println("if (!atGoal_FR)");
            double FR_error = cmd_FR - _FR_motor->getMeanSpeed();
            // Serial.println("Calcul de FR_error");
            // Serial.println(FR_error);
            if(fabs(FR_error)<epsilon_){
                // Serial.println("if fabs(FR_error)<epsilon_)");
                atGoal_FR = true;
                _FR_motor->setPWM(-cmd_FR);
            }
            else{
                _FR_motor->setPWM(computeCommand(2,FR_error));
            }
        //}
        //if(!atGoal_BL){
            // Serial.println("if (!atGoal_BL)");
            double BL_error = cmd_BL - _BL_motor->getMeanSpeed();
            if(fabs(BL_error)<epsilon_){
                atGoal_BL = true;
                _BL_motor->setPWM(cmd_BL);
            }
            else{
                _BL_motor->setPWM(computeCommand(3,BL_error));
            }
        //}
        //if(!atGoal_BR){
            // Serial.println("if (!atGoal_BR)");
            double BR_error = cmd_BR - _BR_motor->getMeanSpeed();
            if(fabs(BR_error)<epsilon_){
                atGoal_BR = true;
                _BR_motor->setPWM(-cmd_BR);
            }
            else{
                _BR_motor->setPWM(computeCommand(4,BR_error));
            }
        //}
        // if(atGoal_FL && atGoal_FR && atGoal_BL && atGoal_BR){
        //     atGoal_ = true;
        // }
    //}
    
}

float PID::computeCommand(int motor_id,double error){
    // Serial.println("computeCommand lancé");
    double eIntegral_;
    switch(motor_id){
        case 1:
            // Serial.println("computeCommand FL_motor");
            eIntegral_FL += error;
            eIntegral_ = eIntegral_FL;
            dt_ = (millis() - lastMeasureTime_FL)/1000.0;
        case 2:
            // Serial.println("computeCommand FR_motor");
            eIntegral_FR += error;
            eIntegral_ = eIntegral_FR;
            dt_ = (millis() - lastMeasureTime_FR)/1000.0;
        case 3:
            // Serial.println("computeCommand BL_motor");
            eIntegral_BL += error;
            eIntegral_ = eIntegral_BL;
            dt_ = (millis() - lastMeasureTime_BL)/1000.0;
        case 4:
            // Serial.println("computeCommand BR_motor");
            eIntegral_BR += error;
            eIntegral_ = eIntegral_BR;
            dt_ = (millis() - lastMeasureTime_BR)/1000.0;
    }
    float CMD;
    
    // Integral saturation
    if(eIntegral_ > eIntegralLim_){
        eIntegral_ = eIntegralLim_;
    }
    if(eIntegral_ < -eIntegralLim_){
        eIntegral_ = -eIntegralLim_;
    }

    switch(motor_id){
        case 1:
            CMD = Kp_*error + Ki_*eIntegral_*dt_ + Kd_*(error-ePrevious_FL)/dt_;
            ePrevious_FL = error;
            lastMeasureTime_FL =  millis();
        case 2:
            CMD = (Kp_*error + Ki_*eIntegral_*dt_ + Kd_*(error-ePrevious_FR)/dt_)*-1;
            ePrevious_FR = error;
            lastMeasureTime_FR =  millis();
        case 3:
            CMD = Kp_*error + Ki_*eIntegral_*dt_ + Kd_*(error-ePrevious_BL)/dt_;
            ePrevious_BL = error;
            lastMeasureTime_BL =  millis();
        case 4:
            CMD = (Kp_*error + Ki_*eIntegral_*dt_ + Kd_*(error-ePrevious_BR)/dt_)*-1;
            ePrevious_BR = error;
            lastMeasureTime_BR =  millis();
    }
    // Serial.println("Sortie de computeCommand");
    // Serial.print("CMD : ");
    // Serial.println(CMD);
    return CMD;
}
void PID::goals(){
    Serial.print("atGoal_ : ");
    Serial.println(this->atGoal_);
    Serial.print("atGoal_FL : ");
    Serial.println(this->atGoal_FL);
    Serial.print("atGoal_FR : ");
    Serial.println(this->atGoal_FR);
    Serial.print("atGoal_BL : ");
    Serial.println(this->atGoal_BL);
    Serial.print("atGoal_BR : ");
    Serial.println(this->atGoal_BR);
}

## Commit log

2022-02-05 Cleaned repo for new project orientation
    [Arduino-Mega.sldprt, BACK.stl, BATTERY.stl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]
2022-02-06 Added CAD of base
    [37d-gearmotor-100-131-150-encoder.SLDPRT, 37d-gearmotor-100-131-150-encoder.step, 545548 assembly.STEP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]
2022-02-09 Finished CAD
    [Base.SLDASM, Bras_001_fixture_joints.SLDPRT, Bras_001_fixture_joints.step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]
2022-02-11 Added dae file of base for simulation
    [Base_CAD.SLDASM, Base_CAD.SLDPRT, Wheel_CAD.SLDASM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]
2022-02-21 New base_joy package, New base_control package, PlatformIO projet for base arduino
    [base.urdf, base.xacro]
2022-02-21 Ajout code moteur + pid
2022-02-21 Ajout de fonctions de démo
2022-02-22 Removed Solidworks files
    [37d-gearmotor-100-131-150-encoder.SLDPRT, 37d-gearmotor-100-131-150-encoder.step, 545548 assembly.STEP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]
2022-02-23 Vision + Calibration
    Calibration de la caméra stéréoscopique. Détection (balle et visage). Cartographie de la disparité stéréoscopique.
2022-02-25 Ajout de l'échiquier + lib perso - CamCSI
2022-02-25 Add README pour la calibration
2022-03-01 ROS library for arduino
    Added only the ROS library for the arduino
2022-03-01 Added message for arduino feedback in ROS library
2022-03-03 Latest ROS arduino library
2022-03-03 Fonctionne avec manette sans PID
2022-03-09 commit pour merge les branches
2022-03-09 Added integration for ros package
    [base.urdf, base.xacro]
2022-03-09 Tested base node and arduino
2022-03-10 Correction, mkdir nested folder
    Pour mkdir, rajouter l'option -p pour creer des nested folders.
2022-03-10 Lib Servo et Bras_servo_control dans ARDUINO
2022-03-10 Revert "Lib Servo et Bras_servo_control dans ARDUINO"
    This reverts commit 3e05e350b24ee18daa49b25bb9b34b000b1eba10.
    [Bras_servo_control.cpp, Bras_servo_control.h]
2022-03-10 Bon push, ajout Bras_lib et Servo_lib dans ARDUINO
2022-03-16 Modification de ros_lib (update ros_lib -> bras_command.msg)
2022-03-16 modification du Cmake pour test de mes codes python
2022-03-16 Correction_message, correction_pins, dsl ca noye
    [main.cpp]
2022-03-23 Node-topics py/arduino fonctionnel de mon coter
    Implementation et test reel est la prochaine etape
2022-03-23 Update bras pins on arduino
2022-03-26 Generate message correction, arduino debug et bras_teleop
    [main.cpp]
2022-03-27 Resolution du probleme avec le topic /rufus/bras_arduino (J'espere)
    ajout de nh.subscribe(bras_sub);
    [main.cpp]
2022-03-30 Vision dans ROS
    [CompressedDepthPublisher.cfg, CompressedPublisher.cfg, CompressedSubscriber.cfg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]
2022-03-30 Arduino marche sans la vidange a jo
2022-03-30 Inverse kinematic et jog manuelle fonctionnelle !!!
2022-04-08 Correction ros_lib, optimisation jogging et tweakage arduino
    [Bras_servo_control.h, main.cpp]
2022-04-08 Chu quasi la, ca noye encore un tsi peu, jvs le jure
2022-04-08 refactor des readme
2022-04-17 ajout des cads
2022-04-17 ajout fab et cad sans zip
    [37d-gearmotor-100-131-150-encoder.SLDPRT, 37d-gearmotor-100-131-150-encoder.step, 545548 assembly.STEP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]
2022-04-17 refactor dossier
    [37d-gearmotor-100-131-150-encoder.SLDPRT, 37d-gearmotor-100-131-150-encoder.step, 545548 assembly.STEP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]
2022-04-19 Update from Jetson

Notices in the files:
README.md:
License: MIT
